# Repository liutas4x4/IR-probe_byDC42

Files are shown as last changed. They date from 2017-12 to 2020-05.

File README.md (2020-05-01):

# Mini differential IR probe for Z axis, for 3D printer
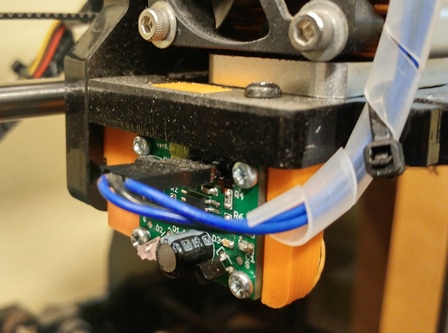
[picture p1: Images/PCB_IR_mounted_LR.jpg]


This is complete set of files to reproduce fork of David Crocker's [Mini Differential IR probe](https://miscsolutions.wordpress.com/mini-height-sensor-board/). Desing is slightly changed. Implemented on Geeetech's acrylic [I3 X clone](https://www.geeetech.com/geeetech-unassembled-prusa-i3-x-3d-printer-diy-kit-p-941.html) of [Prusa I3](https://www.prusaprinters.org/prusa-i3/) 3D printer.

## PCB

It was more quick and cheap to create own PCB for this probe. Gerber files were generated using Spurkfun cam profile, copy is placed in separate directory. [Firmvare](https://github.com/dc42/OrmerodSensorBoard/tree/master/Firmware/Mini-differential-IR/V1.0_1.1) and [schematics](https://github.com/dc42/OrmerodSensorBoard/tree/master/SchematicAndPCB/Mini-differential-IR/V1.0_1.1) used can be found at original DC42's GitHub, version 1.1.

## Holding bracket

The simplest way to attach this probe to acrylic Geeetech's I3 X is to print out modified version of I3B1-31 bracket. Design is done using FreeCAD (v0.15) instead of Solidworks, for GLP purposes. Holes for screws are only 1.8 mm diam, because it is more simple job to drill exact diam for screws you will use instead of correcting CAD file. But if you would like to change something - check [modified bracket](https://github.com/liutas4x4/IR-probe_byDC42/tree/master/I3B1-31-Bracket_modified) directory.

## Connecting

This probe is connected to Z_MIN wires on GT2560. If you version of board has only 2 pins, as mine, connect GND to Ground pin of Z_MIN switch, OUT to second pin. Vcc +5 Volts you can obtain from pin on connector for motor driver.

## Calibration

Very first step - applying firmware code changes to you Marlin. Modified configuration.h and configuration_adv.h can be found at Marlin [there](https://github.com/liutas4x4/Marlin-1.1.X-Geeetech-I3-Pro-X-GT2560). Or you can do modifications you need to your specific Marlin by youself. All things you should do after uploading modified firmware are described at Daviv Crocker's [page](https://miscsolutions.wordpress.com/mini-height-sensor-board/), mentioned above.

#### As for December 23, 2017, BILINEAR and LINEAR autoleveling is not working correctly on Geeetech I3 with Marlin 1.1.6, see Issue [#7860](https://github.com/MarlinFirmware/Marlin/issues/7860) for details. After moving to 1.1.7 BILINEAR nor LINEAR still are not perfect. Under reasearch.

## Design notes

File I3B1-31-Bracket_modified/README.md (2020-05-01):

# CAD files and STL mesh

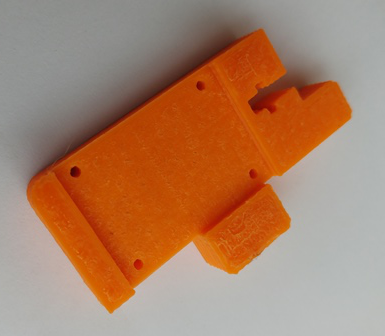
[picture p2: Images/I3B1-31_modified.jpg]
I3B1-31 mod I3B1-31 modified part


Created using FreeCAD v0.15. G-code for lazy ones is included too, but keep in mind: 
there are 230°C hot end temperature and 115°C for table G-code included, for mine ABS 1.75 mm.

Holes for screws are only 1.8 mm diam, because it is more simple to drill exact diam for screws you will use instead of correcting CAD file. But if you would like to change something, you are free to do it.

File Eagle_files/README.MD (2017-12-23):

# Eagle files for IR Z probe
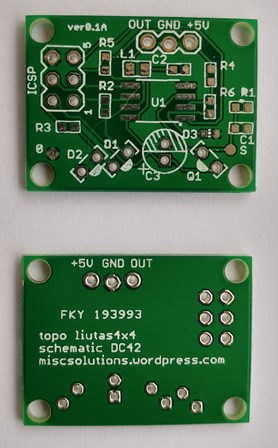
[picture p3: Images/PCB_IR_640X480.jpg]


#### CAUTION: On photo you see PCB version 0.1A with wrong silkscreen marks of +5V and OUT pins. At version 0.1B there on GitHub is set of correct files.

Eagle 8.5.1 was used. Keep in mind, PCB was created using SeeedStudio and Sparkfun Eagle libraries connected. CAM job file is in the [separate directory](https://github.com/liutas4x4/IR-probe_byDC42/tree/master/cam_for_Eagle).

There are also all [Gerber files](https://github.com/liutas4x4/IR-probe_byDC42/tree/master/Gerber_files) ready for PCB ordering.

File BOM_to_Mouser.xlsx contains list of all parts used (BOM) with link to Mouser, except GL480E IR diodes.

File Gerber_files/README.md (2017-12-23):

# Gerber files for IR Z probe

CAM job file is in separate directory. Originally, PCB was printed using SeeeStudio PCB service.

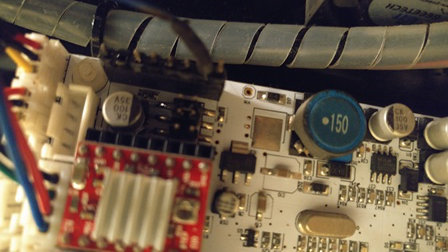
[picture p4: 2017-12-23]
Images/Connection_5V.jpg

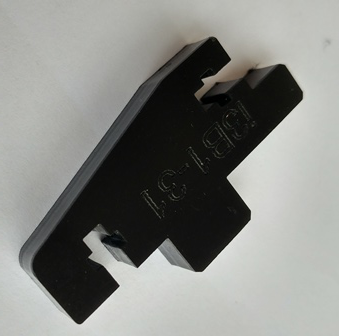
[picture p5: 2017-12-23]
Images/I3B1-31_original.jpg

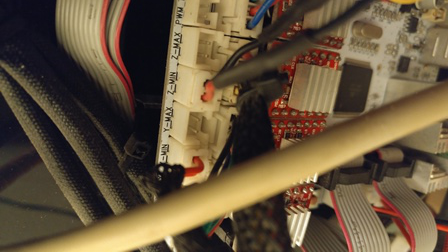
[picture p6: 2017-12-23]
Images/Connection_GND_OUT.jpg

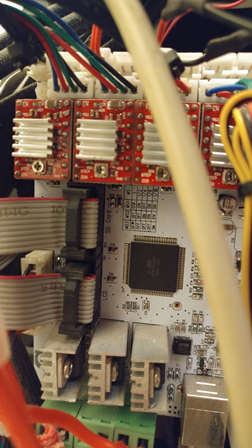
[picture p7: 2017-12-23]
Images/Noname_GT2560.jpg

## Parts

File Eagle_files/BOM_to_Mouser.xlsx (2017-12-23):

Select | Product Detail |  | Customer Part No. | Order Qty.
 | Mouser No: | 81-GRM39C102J50 (https://www.mouser.co.il/productdetail/81-grm39c102j50) |  | 10
 | Mfr. No: | GRM1885C1H102JA01D (https://www.mouser.co.il/productdetail/81-grm39c102j50)
 | Desc.: | Multilayer Ceramic Capacitors MLCC - SMD/SMT Multilayer Ceramic Capacitors MLCC - SMD/SMT 0603 1000pF 50volts C0G 5% (https://www.mouser.co.il/productdetail/81-grm39c102j50)
 | Mouser No: | 80-C0603C104K5REAUTO (https://www.mouser.co.il/productdetail/80-c0603c104k5reauto) |  | 10
 | Mfr. No: | C0603C104K5RECAUTO (https://www.mouser.co.il/productdetail/80-c0603c104k5reauto)
 | Desc.: | Multilayer Ceramic Capacitors MLCC - SMD/SMT Multilayer Ceramic Capacitors MLCC - SMD/SMT 50volts .1uF 10% X7R AUTO ESD (https://www.mouser.co.il/productdetail/80-c0603c104k5reauto)
 | Mouser No: | 667-ECE-A1CKA101 (https://www.mouser.co.il/productdetail/667-ece-a1cka101) |  | 10
 | Mfr. No: | ECE-A1CKA101 (https://www.mouser.co.il/productdetail/667-ece-a1cka101)
 | Desc.: | Aluminium Electrolytic Capacitors - Leaded Aluminium Electrolytic Capacitors - Leaded 100uF 16V (https://www.mouser.co.il/productdetail/667-ece-a1cka101)
 | Mouser No: | 70-ILSB0805ER1R0K (https://www.mouser.co.il/productdetail/70-ilsb0805er1r0k) |  | 10
 | Mfr. No: | ILSB0805ER1R0K (https://www.mouser.co.il/productdetail/70-ilsb0805er1r0k)
 | Desc.: | Fixed Inductors Fixed Inductors 1uH 10% (https://www.mouser.co.il/productdetail/70-ilsb0805er1r0k)
 | Mouser No: | 720-LRQ396P1Q21 (https://www.mouser.co.il/productdetail/720-lrq396p1q21) |  | 10
 | Mfr. No: | LR Q396-P1Q2-1 (https://www.mouser.co.il/productdetail/720-lrq396p1q21)
 | Desc.: | Standard LEDs - SMD Standard LEDs - SMD Red, 624nm (https://www.mouser.co.il/productdetail/720-lrq396p1q21)
 | Mouser No: | 720-SFH3100F (https://www.mouser.co.il/productdetail/720-sfh3100f) |  | 10
 | Mfr. No: | SFH 3100 F (https://www.mouser.co.il/productdetail/720-sfh3100f)
 | Desc.: | Phototransistors Phototransistors PHOTOTRANSISTOR (https://www.mouser.co.il/productdetail/720-sfh3100f)
 | Mouser No: | 556-ATTINY25-20SSU (https://www.mouser.co.il/productdetail/556-attiny25-20ssu) |  | 10
 | Mfr. No: | ATTINY25-20SSU (https://www.mouser.co.il/productdetail/556-attiny25-20ssu)
 | Desc.: | 8-bit Microcontrollers - MCU 8-bit Microcontrollers - MCU 8-bit 5V 20MHz (https://www.mouser.co.il/productdetail/556-attiny25-20ssu)
 | Mouser No: | 667-ERJ-U03F1200V (https://www.mouser.co.il/productdetail/667-erj-u03f1200v) |  | 10
 | Mfr. No: | ERJ-U03F1200V (https://www.mouser.co.il/productdetail/667-erj-u03f1200v)
 | Desc.: | Thick Film Resistors - SMD Thick Film Resistors - SMD 0603 1% 120ohm Anti-Sulfur AEC-Q200 (https://www.mouser.co.il/productdetail/667-erj-u03f1200v)
 | Mouser No: | 667-ERJ-U03F1500V (https://www.mouser.co.il/productdetail/667-erj-u03f1500v) |  | 10
 | Mfr. No: | ERJ-U03F1500V (https://www.mouser.co.il/productdetail/667-erj-u03f1500v)
 | Desc.: | Thick Film Resistors - SMD Thick Film Resistors - SMD 0603 1% 150ohm Anti-Sulfur AEC-Q200 (https://www.mouser.co.il/productdetail/667-erj-u03f1500v)
 | Mouser No: | 667-ERJ-U03F1202V (https://www.mouser.co.il/productdetail/667-erj-u03f1202v) |  | 10
 | Mfr. No: | ERJ-U03F1202V (https://www.mouser.co.il/productdetail/667-erj-u03f1202v)
 | Desc.: | Thick Film Resistors - SMD Thick Film Resistors - SMD 0603 1% 12Kohm Anti-Sulfur AEC-Q200 (https://www.mouser.co.il/productdetail/667-erj-u03f1202v)
 | Mouser No: | 667-ERJ-U03F6801V (https://www.mouser.co.il/productdetail/667-erj-u03f6801v) |  | 10
 | Mfr. No: | ERJ-U03F6801V (https://www.mouser.co.il/productdetail/667-erj-u03f6801v)
 | Desc.: | Thick Film Resistors - SMD Thick Film Resistors - SMD 0603 1% 6.8Kohm Anti-Sulfur AEC-Q200 (https://www.mouser.co.il/productdetail/667-erj-u03f6801v)
 | Mouser No: | 667-ERJ-U03F3300V (https://www.mouser.co.il/productdetail/667-erj-u03f3300v) |  | 10
 | Mfr. No: | ERJ-U03F3300V (https://www.mouser.co.il/productdetail/667-erj-u03f3300v)
 | Desc.: | Thick Film Resistors - SMD Thick Film Resistors - SMD 0603 1% 330ohm Anti-Sulfur AEC-Q200 (https://www.mouser.co.il/productdetail/667-erj-u03f3300v)
 | Mouser No: | 603-RC0603FR-0710KL (https://www.mouser.co.il/productdetail/603-rc0603fr-0710kl) |  | 10
 | Mfr. No: | RC0603FR-0710KL (https://www.mouser.co.il/productdetail/603-rc0603fr-0710kl)
 | Desc.: | Thick Film Resistors - SMD Thick Film Resistors - SMD 10K OHM 1% (https://www.mouser.co.il/productdetail/603-rc0603fr-0710kl)

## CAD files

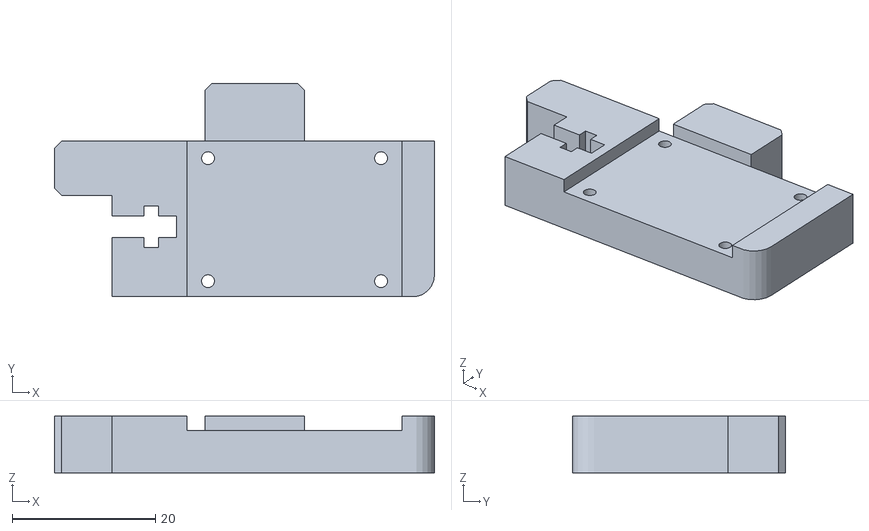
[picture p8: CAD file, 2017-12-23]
I3B1-31-Bracket_modified/i3B1-31 with IR probe PCB Holder.stl
53.0 x 29.7 x 7.90

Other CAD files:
I3B1-31-Bracket_modified/i3B1-31 Bracket With IR differential probe holder.FCStd

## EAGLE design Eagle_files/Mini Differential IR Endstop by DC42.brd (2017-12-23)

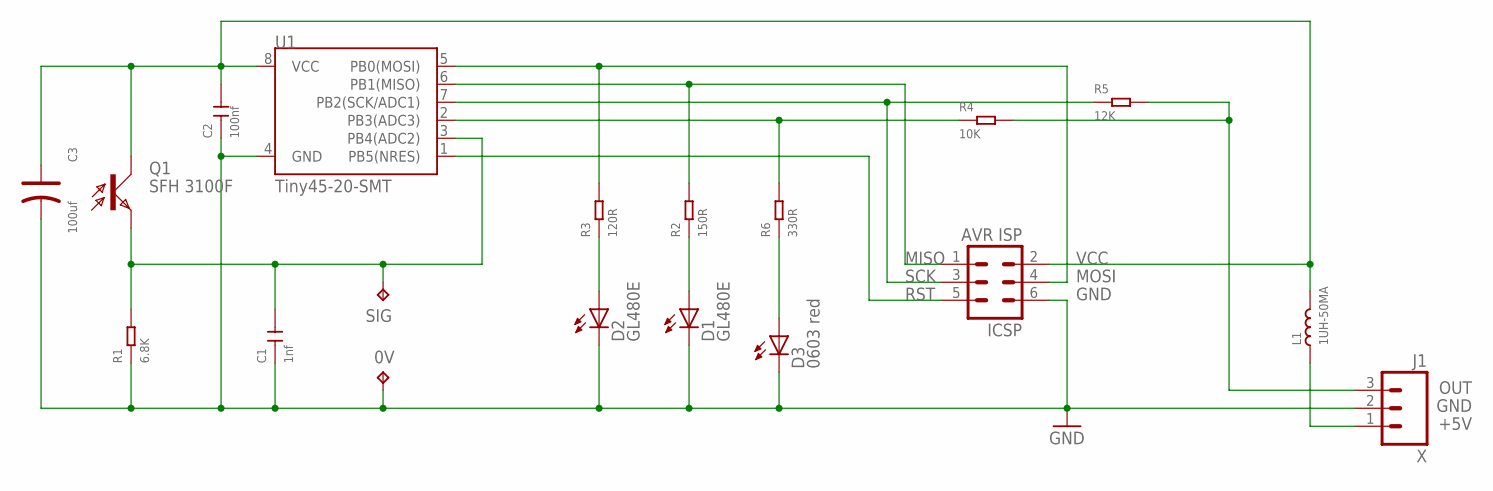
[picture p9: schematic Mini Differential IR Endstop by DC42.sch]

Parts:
0V: TPB1,27; B1,27
C1: 1nf; C0603
C2: 100nf; C0603
C3: 100uf; PC-D5.3MM
D1, D2: GL480E; IRL80A
D3: 0603 red; CHIP-LED0603
ICSP: AVR ISP; MA03-2
J1: X; 1X03_LOCK
L1: 1UH-50MA; L0805
Q1: SFH 3100F; SIDELOOKER
R1: 6.8K; R0603
R2: 150R; R0603
R3: 120R; R0603
R4: 10K; R0603
R5: 12K; R0603
R6: 330R; R0603
SIG: TPB1,27; B1,27
U1: Tiny45-20-SMT; SO08-EIAJ

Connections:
+5V: J1.1, L1.1
GND: 0V.TP, C1.1, C2.1, C3.-, D1.K (C), D2.K (C), D3.C, ICSP.6, J1.2, R1.1, U1.4 (GND)
MISO: ICSP.1, R2.2, U1.6 (PB1(MISO))
MOSI: ICSP.4, R3.2, U1.5 (PB0(MOSI))
unnamed: R4.1, R6.2, U1.2 (PB3(ADC3))
unnamed: D1.A, R2.1
unnamed: D2.A, R3.1
unnamed: D3.A, R6.1
unnamed: C1.2, Q1.K (E), R1.2, SIG.TP, U1.3 (PB4(ADC2))
OUT: J1.3, R4.2, R5.2
RST: ICSP.5, U1.1 (PB5(NRES))
SCK: ICSP.3, R5.1, U1.7 (PB2(SCK/ADC1))
VCC: C2.2, C3.+, ICSP.2, L1.2, Q1.A (C), U1.8 (VCC)

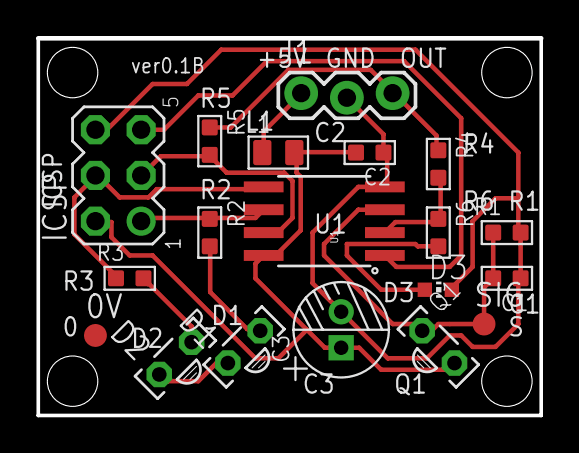
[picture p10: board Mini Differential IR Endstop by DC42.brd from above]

Board: 2 copper layers, 27.9 x 21.0 mm, 19 parts (0 on the bottom side), 13 nets.

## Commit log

2017-12-23 Ver 0.1B
    Complete Eagle and Gerber files.
    [Mini Differential IR Endstop by DC42.brd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]
2017-12-23 Holder for IR probe
    Open FreeCAD, stl and Gcode.
    [i3B1-31 Bracket With IR differential probe holder.FCStd, i3B1-31 with IR probe PCB Holder.stl]
2017-12-26 1.1.7 still not does BILINEAR correctly.
    It is possible, that for version 1.1 of IR probe, while measurement error is in acceptable range by M48 test in particular point, is mot tolerant to uneven IR properties of borosilicate glass and it's underneath.

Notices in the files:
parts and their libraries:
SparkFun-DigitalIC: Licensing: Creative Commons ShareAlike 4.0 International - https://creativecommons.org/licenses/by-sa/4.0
